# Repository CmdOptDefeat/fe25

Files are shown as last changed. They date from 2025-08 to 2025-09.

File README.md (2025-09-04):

<picture>
  <source media="(prefers-color-scheme: dark)" srcset="https://github.com/CmdOptDefeat/fe25/blob/main/repo-assets/logo/ctrlaltdefeat-no-glow-no-bg-4096.png">
  <source media="(prefers-color-scheme: light)" srcset="https://github.com/CmdOptDefeat/fe25/blob/main/repo-assets/logo/ctrlaltdefeat-no-glow-no-bg-dark-4096.png">
  CTRL+ALT+DEFEAT Logo (updates based on your theme!)
</picture>

<br><br>Welcome to the repository for our entry in the WRO Future Engineers 2025 competition!
We are a team of 2 aspiring engineers building an autonomous robotic car using Raspberry Pi 5 & RP2040, equipped with various sensors and custom designs.

# About the Team
Adbhut Patil: Adbhut is studying in 10th grade, under NIOS. He is interested in robotics, programming, and aviation.

Pranav Kiran Rajarathna: Pranav is currently studying in the 11th grade(PCMC combination) and has been interested in Robotics for several years . He has participated in WRO in other categories in the past years. He was also part of Coding club in his school and built a few robotics projects for school events. His other interests include maths, physics, numismatics and history.

| __Team Photo__ |
|:-----------:|
|Team Photo|
| __Picture: Pranav (Left) and Adbhut (Right)__ |

# Project Overview
This project is our official entry for the Future Engineers category at the World Robot Olympiad 2025. Our goal is to construct a self-driving vehicle capable of navigating the track in both the Open and Obstacle Rounds. The programs are written in C++ and Python in the VSCode IDE, with the PlatformIO extension. OpenCV is used with the Raspberry Pi for object detection and navigation. This repository contains the programs, hardware description, schematics and design files of our solution.

Note: The whole readme file is massive.
See [this section](https://github.com/CmdOptDefeat/fe25?tab=readme-ov-file#peripherals-interface-board) for more details about the peripherals interface board, and [this section](https://github.com/CmdOptDefeat/fe25?tab=readme-ov-file#raspberry-pi-system) for details about the RPi 5 and its setup. [System architecture](https://github.com/CmdOptDefeat/fe25?tab=readme-ov-file#system-architecture) includes information about the [robot and mobility](https://github.com/CmdOptDefeat/fe25?tab=readme-ov-file#mobility), [power system](https://github.com/CmdOptDefeat/fe25?tab=readme-ov-file#power), [sensors](https://github.com/CmdOptDefeat/fe25?tab=readme-ov-file#sensors), [obstacle management](https://github.com/CmdOptDefeat/fe25?tab=readme-ov-file#obstacle-management) and [parking and unparking](https://github.com/CmdOptDefeat/fe25?tab=readme-ov-file#unparking-and-parking).

Some photos of the robot - 
<br><br>
Top view
Side view
<br><br>
All photos may be found [here](https://github.com/CmdOptDefeat/fe25/tree/main/repo-assets/raw-photos/robot)

# Hardware Components
- __Compute:__ Raspberry Pi 5 (main computer), Raspberry Pi 2040 (Waveshare RP2040-Zero, real-time control)
- __Sensors:__ 1D LiDAR, IMU, rotary encoders, Picamera
- __Actuators:__ N20 geared DC motor with encoder, MG996R 180° servo
- __Chassis:__ Commercially available base with 3D-printable additions (3D-design files included)
- __Electronics:__ Custom peripherals interface PCB for reliable connections to sensors

# Repository Structure
- [design-files](https://github.com/CmdOptDefeat/fe25/tree/main/design-files) : Contains the Bill of Materials, 3D-printable design files and hardware. 
- [initial-tests](https://github.com/CmdOptDefeat/fe25/tree/main/initial-tests) : Intial tests on various sensors to ensure accurate data collection and basic object detection algorithm.
- [hw](https://github.com/CmdOptDefeat/fe25/tree/main/hw) : Contains schematic and PCB files for the peripherals interface board.
- [sw](https://github.com/CmdOptDefeat/fe25/tree/main/sw) : Contains PlatformIO project for the peripherals interface board.
- [open-round](https://github.com/CmdOptDefeat/fe25/tree/main/open-round) : It contains the program files for the open round over various iterations and hardware setups. The final open round program is found in `sw/peripherals-board/src/divers`
- [repo-assets](https://github.com/CmdOptDefeat/fe25/tree/main/repo-assets) : It contains pictures and description of the robot and its components. All other photos in the repo are also found here.
- [obstacle-round](https://github.com/CmdOptDefeat/fe25/tree/main/obstacle-round) : Programs for the obstacle round. These are categorised in order of working alphabetically. The related videos and log files are also present in these folders.
- [test-data-recordings/open-round](https://github.com/CmdOptDefeat/fe25/tree/main/test-data-recordings) : It contains data logs from various open round tests

> [!NOTE]
> Random files called `.lgd-nfy0` may be seen sometimes in varioues places. These were probably created by a typo a long time ago, and despite repeated deletion, they keep spawning everywhere in the Pi's clone of the repo! Just ignore them, if they occur. 
> `.DS_Store` are some system files used on MacOS. These too may appear throughout the repo, and may be ignored.

# System Architecture 

-	Raspberry Pi 5: It uses opencv and serial to handle the complex tasks of object detection and navigation.
-	RP2040 (Pi Pico): Handles real-time tasks (motor PID, encoder feedback, servo control, IMU, 1D LiDAR)
-	LiDARs: Used for detecting turn direction and executing turns and in parking
-	IMU: Gives yaw (and other orientations) of the robot in [0,360) clockwise
-	Motor/Servos: PWM and PI controls respectively for movement using sensor data, coordinated by the RP2040

## Mobility

- A commercially available metal [chassis base](https://www.elecrow.com/4wd-smart-car-robot-chassis-for-arduino-servo-steering.html) has been used with custom designed and printed parts. This chassis was selected mainly for its good steering system, mobility and customisabilty (there are lots of through holes through the base-frame). While the steering was retained, the remaining parts were custom designed.
- A link based steering system is used in the robot with a link-rod between the front wheel joints and another between a wheel joint and the servo. This steering system has been taken from the chassis without much modification due to its precision. A MG996R 180° servo has been used for the steering due to its high torque and accuracy, which improve mobility. The turn radius is around 32-33cm.
- Steering System
- A single axle rear drive train is used for driving is used. A 200RPM N20 motor is used due to its speed and decent torque. A 1:1 gear ratio is used with a pair of brass gears. Bearings are used on the rear axle for smooth movement. A custom [rear drive holder](https://github.com/CmdOptDefeat/fe25/blob/main/design-files/N20%20Motor%20Holder.stl) is used to house all these parts.
- Both the servo and N20 motors are connected to the peripherals board. The servo is controlled using the standard library, while PWM is used for speed control of the motor.
- Rear Drive
- This robot offers realistic car-like dynamics, ideal for FE challenge simulation.
[Design files](https://github.com/CmdOptDefeat/fe25/tree/main/design-files) contains all the other custom 3D-Design files (created on [TinkerCAD](https://www.tinkercad.com)) for mounting various compnents and systems onto the base chassis and one another.
[Robot assembly](https://github.com/CmdOptDefeat/fe25?tab=readme-ov-file#robot-assembly) instructions are below.
- Improvements: 
1. A uniform steering system. In the current model, the servo has to turn a greater angle left than right for the same angles of the wheels in each direction. This complicates driving algorithms to some extent. A better, but equally smooth steering system, maybe a rack-and-pinion, will solve these issues.
2. Better gear train. The current gears, though made of brass wear down quite easily for some unidentified reason. This causes slipping if there is more wear.
3. Reducing the turning radius. The current bot, while quite manoeuvrable has a large turn radius (almost 33-34cm). Reducing this would make taking tighter turns possible, improving error margins in the obstacle round. This can be done by bringing the drive train forward.

## Power

- A [Waveshare UPS Hat E](https://www.waveshare.com/wiki/UPS_HAT_(E)) is used for powering the robot. It uses 4 4000mAH 3.6V 21700 Li-ion batteries. (Different battery capacities may be used). All outputs are at 5V.
- The Pi is powered at a stable 5V via the POGO pins on the UPS Hat. The PiCamera and RPLidar are power from the Pi.
- The RP2040 and all connected sensors are powered through a USB A-C cable from the Pi to it.
- The total current draw for the obstacle round is around 600-630mA, and around 250-300mA for idle with the Pi.
- The peripherals board gets power directly from the UPS Hat through a USB-A cable that has been cut to get the power wires. This powers only the rear motor and steering servo.
- Improvements:
1. The UPS Hat that we are using has a weird anomaly. Although the batteries will have good voltage output and detected capacity, it will show the net remaining capacity to be very low. We have edited the code of the UPS library to not allow it run `sudo poweroff` when it misdetects such a situation.
Additiionally, charging of batteries when the Pi is off does not seem to be detected. 

## Sensors

- __TFLuna LiDAR:__ These are 1D-LiDARs that are used to measure distances to the front, left, right (for driving) and back(parking) of the robot. They are connected to the RP2040. A separate section has been designed at the front of the robot to house all four LiDARs. Each LiDAR has 5 wires, grouped into 4+1 (I2C + GND) going into the peripherals board. These LiDARs were selected for their accuracy, small size and ease of use.
- __BNO055:__ This is the IMU we are using for orientation due to its reliability, accuracy and simplicity of use. It is connected to the RP2040, and is directly slotted into the peripherals board.
- __nRF24L01:__ This is the wireless module used for wireless communication during testing and debugging with the RP2040. Another custom module (telemetry board) is made for receiving the data. (Note : This is not plugged in for actual rounds). It is directly slotted into the peripherals board.
- __Motor encoders:__ The encoders give ticks each time they are trigerred by rotation of the motor shaft. Data from it is used for distance calculations. In our case, about 43 ticks corresponds to 1cm. The 4 encoder wires are grouped together and connected to the peripherals board.
- __Raspberry Pi Camera Module 3 Wide:__ It is used with the Pi for detecting the an obstacles. The camera is secured at four points for greater stability. With only two connection points, the camera could be easily turned due to the material properties of the Camera to Pi 5 connection wire. The higher mounting location allows it to detect obstacles from a large distance (almost 2m!) and plan accordingly. The Wide lens allows for a greater field of view. The NoIR version used to give odd red patches due to the lack of the IR filter in some test cases.
- Improvements: 
1. The 1D LiDARs are quite expensive. Ultrasonic sensors would have done for the sides.
2. The BNO055 does clock stretching, which causes issues on the I2C buses of most microcontrollers (thankfully not the RP2040). It also has a slight drifting tendency of a few degrees after a round. A IMU that does not have these issues and is easy to use will be more accurate and more flexible in use.

The [Bill of Materials](https://github.com/CmdOptDefeat/fe25/blob/main/design-files/Bill%20of%20Materials.md) contains all necessary parts/components and their sources.

## Obstacle Management

- This is done mainly using the camera feed from the PiCamera 3 Wide. The NoIR version tends to give red spot in places with lots of light due to lack of IR filter, which made it incompatible for this case.
- The obstacle management sections were not able to be integrated with one another in time, but the various sections do work independently.
- The OpenCV library (in Python3) is used for all the image manipulation and data extrapolation. HSV mode has been used for all the detecting, while images arer displayed in RGB. Sometimes, red may appear as blue due to use of BGR format used by camera to record. This is of no consequence, since it does not affect detection itself.
- Initially, the colour ranges for the obstacles, parking walls and side walls are identified. Interestingly, in our case, the 'magenta' parking walls show up as pure red.
- First, the region of interest (ROI) is taken as the bottom half of the feed (this is for our camera placement. May vary for other setups).
- Then, coloured masks (one each for red and green) are applied, followed by OpenCV's controur detection to detect surfaces. Data like position, height and width of the contours may be obtained from the other OpenCV methods.
- If the contours detected meet the required criteria (like size, height-width ratio), they are classified as obstacles. For our benefit, rectangles are drawn around the obstacles.
- The basic idea is to treat both possible positions in a row of the 2x3 grid as the same (calculations use the actual values). This greatly simplifies tthe program, since only the outer and inner lanes are used for the driving, while the middle lane is used only for switching between the other two.
- Using the data available, including obstacle position, yaw and distance travelled, the required steering is calculated to pass the obstacle on the correct side, when not at a turn (Red - right, green - left) on a linear scale
- For turns:
1. Starting closer to the inner wall: The seen obstacle before the turn is considered. If turn must to taken sticking to the inner wall, it is immediately taken. If the turn must be taken to get closer to the outer wall, a curve(like a question-mark) is followed. If there is another obstacle of the opposite colour, then the robot the goes back some distance to be able to do the manoeuvre.
2. Starting closer to the outer wall: A turn is taken, making it align with the middle lane. Following this, the robot manoeuvres based on the obstacle/s present.
3. In case of the parking wall being there on every 4th turn, the turning and linear coefficients are changed to get the robot to turn to the adjusted lanes and obstacle position.

Improvements:
1. The RPLidar might have been used effectively with better drivers with the standard Raspbian OS.
2. A smaller robot would have been more agile, making both turning and straight section navigation much easier.
3. Having the axles closer would enable for tighter turns.

## Getting out of the parking lot
Getting out of the parking lot (fondly referred to as "unparking") is handled by the peripherals interface board. The vehicle takes three turns to orient itself so it is perpendicular to the parking lot, and then backs up into the parking lot. It then transfers control to the Raspberry Pi.

## Parallel parking
Parking is also handled by the peripherals interface board. The Raspberry Pi hands over control after the last obstacle. The algorithm takes the following steps:
- Move backwards until the vehicle is abeam the parking lot
- Turn and move backwards and move into the parking lot
- Move forwards so that the next turn can be made
- Turn and move backwards into the parking lot
- Move forwards and turn until the vehicle is parallel to the parking lot

# Robot Assembly

It will be helpful to refer to the [pictures of the construction](https://github.com/CmdOptDefeat/fe25/tree/main/repo-assets/raw-photos/assembly) while building. Most screws used are of 3M type (3mm dia.). At some places in our robot, internal hex screws are used in places where plus(+) screws of the right length were not available.
1. Add the front wheels and steering link to the robot
2. Attach the servo motor and connect it to the steering link
3. Print all design files
4. Attach the N20 motor onto the rear drive with brackets. Fit a gear onto the motor.
5. Cut the rear axle to the appropriate length (around 96mm) and attach the rear axle with wheels and gear onto the rear drive.
6. Mount the rear drive onto the chassis.
7. Attach 6 pillar screws of length 26mm in the back and 2 of length 22mm in the front (adjacent to the servo)
8. Attach the middle plate at the 6 rear points, but not at the front. The peripherals board may be screwed on using 4 pillar screws.
9. Attach the TFLuna LiDARs to the front LiDAR holder section.
10. Attach the LiDAR holder section to the front of the chassis.
11. Attach the additional support section (this used to be used when the RPLidar was also attached to the model) to the 2 front middle plate points and 2 rear RPLidar points.
13. Attach the two PiCamera holder parts to the rear of the support section, and screw in the camera (2M screws and nuts are needed)
12. Attach the top-most Raspberry Pi and UPS platform to the rear with screw pillars.
13. Attach the rear lidar holder with the rear lidar attached to it
14. Attach the Raspberry Pi with the UPS Hat to the top.
15. Make all wired connections by referring to schematic files.

# Peripherals Interface Board
Peripherals Interface Board - Top

The peripherals interface board goes between the Raspberry Pi and vehicle hardware. The board talks to three 1d TFLuna LiDARs, a 9-axis BNO055 IMU, the motor encoder, the drive motor, and the steering servo. It talks to the Pi over USB.

Peripherals Board on the Robot

## Hardware
The board is a two-layer, 1.6 mm thick PCB designed in [KiCad](https://kicad.org) and manufactured by [Robu](https://robu.in).
TODO: Expand

## Software
The interface board was programmed in C++, with the C++ SDK from Raspberry Pi for the RP2040 chip. Code was compiled and flashed with the PlatformIO extension for Visual Studio Code.

The codebase is designed to be modular, with easily swappable drivers for hardware abstraction. Algorithms do not need to know about specific hardware protocols or constraints

`main.cpp` loads in drivers, which implement virtual interface classes. `main.cpp` then initialises everything, and in a loop, gets data from the `SensoorManager`, passes that data to our drive algorithm, and outputs it to the `TargetController`, which commands the motor and steering servo.
Drivers are in `/src/drivers`, Interfaces are in `/src/interfaces/`, and utilities are in `/src/utils/`.

### Code Development Standards
To ensure easily testable, upgradeable, and clean code, the following standards were decided for writing code for the interface board.
> [!NOTE]
> Due to time constraints, not all of these could be adhered to during final development

- `main.cpp` must be as clean as possible.
- Logic and code flow must be easy to understand.
- All hardware-specific things should be done inside a driver.
- Drivers must take in a standard unit as their input.
- Drivers must not take in [magic numbers](https://en.wikipedia.org/wiki/Magic_number_(programming)).

### Drivers
> [!NOTE]
> Hardware revision 1 drivers are incomplete, as the peripherals baord codebase was partly written when the switch from the prototype interface and the PCB occured, and drivers from that point on were only for the PCB (hardware revision 2).

A list of implemented drivers:
- `hwrev2_imu` : Implements `ISensor`. Driver for the BNO055. Gets orientation data processed by the BNO055's internal microcontroller.
- `hwrev2_lidar` : Implements `ISensor`. Driver for the TFLuna LiDARs. Returns a [0, 359] of distance data. The three LiDARs are mapped to `0`, `90`, and `270`. (This is a remnant of the original plan of connecting the RPLidar to the peripherals board, instead of to the Pi.)
- `hwrev2_motor_driver` : Implements `IMotorDriver`. Driver for the TB6612FNG dual-channel H-bridge motor driver. The driver only supports driving a single channel on the T66612FNG.
- `hwrev2_rf24_communication` :  Implements `ICommunication`. Driver for the nRF24L01+ radio used during development. Transmits vehicle data and gets commands from another nRF24L01+, connected to a computer.
- `hwrev2_single_lidar_open_round` : Implements `IDriveAlgorithm`. A port of our open round test algorithm. The name is misleading, the algorithm uses all three TFLunas.
- `hwrev2_steering_driver` : Implements `ISteeringDriver`. Driver for the MG996 steering servo. Takes in a degree input and coverts it to a 0-180 command with a conversion constant.
- `hwrev2_target_control` : Implements `ITargetControl`. Takes in a `VehicleCommand`, and either passes it directly through to the `ISteeringDriver` and `IMotorDriver`, or passes the command through a PID controller first.
- `hwrev2_uart_logger` :  Implements `ILogger`, Takes in a sender, message type, and a message string
- `hwrev2_vehicle_speed` : Implements `ISensor`. Gets vehicle distance from the motor encoder. Calculates speed using time between pulses.
  TODO: unparking and parking drivers

### Interfaces

Interfaces are virtual classes which define certain functions. Drivers implement these classes. Code calls functions defined in the virtual interface class.

- `IDriveAlgorithm` : Takes in a `VehicleData` object, and returns a `VehicleCommand` object.
- `ILogger` : Constructs a message and prints it out on a UART bus. Takes in a sender string, a log type (information, warning, error) and the message.
- `IMotorDriver` : Takes in a speed value and outputs to a motor driver.
- `ISensor` :  A generic sensor object. Returns a vector of `SensorData` objects.
- `ISteeringDriver` :  Takes in a wheel steering angle, outputs to a steering mechanism.
- `ITargetControl`: Takes in a `VehicleCommand`, outputs to a motor and steering driver.

### Managers

Managers are classes that handle certain aspects of the vehicle. Certain structs have their header files in the `/src/managers` folder, even though they are not classes.

- `VehicleConfig` :  A struct containing information about the vehicle. A `VehicleConfig` struct is passed to all drivers asnd managers.
- `SensorData` :  A struct containing fields for all data that can be collected by the vehicle, and an enum which tells the caller what fields are being used.
- `SensorManager` :  A class which takes in an arbitrary number of sensors, collects data from them, and processes them into a `VehicleData` struct.
- `SensorStatus` :  A (currently unused) enumeration which defines keys for states a sensor can be in. 
- `Vec3f` :  A struct of three double-precisionn floating point numbers, used to represent three-axis values.
- `VehicleCommand` :  A struct defining a target speed and yaw value for the vehicle. Returned by a drive algorithm, passed to a `ITargetController`.
- `VehicleData` :  A struct containing processed vehicle data. Returned by a `SensorManager`.

## Utilities

- `SchedulerTask` : A class which calls a function periodically.
- `Schedular` : A class which takes in an arbitrary number of `SchedulerTask`s, and updates them.

# Raspberry Pi System

The Raspberry Pi system handles most tasks for the obstacle round, including unparking, obstacle detection and navigation.
TODO: it doesn't handle unparking, update this section

## Raspbian Setup

We are using Raspbian Bookworm on the Raspberry Pi (latest at the time of this project)
Run the following commands in the terminal
- $`sudo chmod 0700 /run/user/1000`
- $`sudo apt install software-properties-common`
- $`sudo apt install python3-launchpadlib`
- $`sudo apt install code`
- $`sudo apt upgrade code`
- $`sudo apt install idle3`
- $`sudo apt install python3-opencv`
- $`sudo apt install -y python3-libcamera python3-pyqt5 python3-picamera2`
- Test camera library installation with $`rpicam-hello`
- Refer [here](https://www.waveshare.com/wiki/UPS_HAT_(E)) to install UPS Hat library to see details about the batteries etc.
- If the Pi is accidentally shut down, and git is not working, run the following commands: 
1. $`find .git/objects/ -type f -empty | xargs rm` - Cleaning
2. $`git fetch -p` - Restore missing objects
3. $`git fsck --full` - Verify
- It is advised to have RPiConnect for easy connection to the Pi.
- This reposittory is cloned on the Pi and the obstacle round program is added to the startup sequence.

## Adding Programs to Startup

The method used here involves running executables on startup. Refer [`initial-tests/startup-test/`](https://github.com/cmdoptdefeat/fe25/tree/main/initial-tests/startup-test) for the code.
1. Create the python file
2. Create a launcher script, like the one in the initial test file, that ends in `.sh`. Ensure the launcher is working with `./(launcher-name).sh` in its directory.
3. In the launcher script, navigate to the directory of the python file and run it with `sudo python3 (file-name).py`. Then return to user directory
4. In the directory with launcher script, make it executable by running `sudo chmod 755 (launcher-name).sh`
5. Run `sudo crontab -e` (you can use nano to edit it), and add `@reboot sh /home/(user)/(path to launcher)/(launcher-name).sh` at the end.
6. Restart the Pi (`sudo reboot`) to check if it works. 

## PiCamera 3

The Raspberry Pi Camera Module 3 Wide is used for obstacle detection. It is placed high up to have a good view. (We actually only use the bottom half of the frame!) It is connected to port 0.

## Serial Communication

The Pi communicates with the RP2040 over the serial. When the Pi sends a command (speed and steering), the RP2040 sends back data (like yaw, lidar distance, turn direction etc.) The RP2040 is connected to a USB port of the Raspberry Pi and is recognised by its ID.

# Open Round

Refer to [`sw/peripherals-board/src/drivers/hwrev2/hwrev2_single_lidar_open_round.cpp and .hpp`](https://github.com/CmdOptDefeat/fe25/blob/main/sw/peripherals-board/src/drivers/hwrev2/hwrev2_single_lidar_open_round.cpp) files for program.
The idea to stick to the outer wall, so even with randomisation, the extended inner wall is not hit.

Videos of the open round may be found [here](https://github.com/CmdOptDefeat/fe25/tree/main/repo-assets/open-round-videos)

- Uses front LiDAR to detect when to start a turn (if obstacle is close).
- Decides turn direction (left/right) based on side LiDARs (First turn only)
- Turns are started considering factors of distance available, yaw, current section and distance travelled. 
- Adjusts steering (servo position) during turn based on yaw and for greater smoothness.
- Target yaw and threshold distance may be altered for better accuracy and counter drifting.
- When not turning, PI controller is used with yaw to follow a straight path accurately.
- Counts turns; after 12 turns (3 rounds), slows down and stops at the start section.

## Flow
1. Start moving straight.
2. Decide turn direction using side LiDARs. (For first turn only)
3. Detect distance to wall ahead with front LiDAR.
4. Execute turn when condition are met, adjust steering and target yaw.
5. After turn, resume straight movement with PI control.
6. Repeat for 3 rounds (12 turns).
7. After final round, slow down and stop in the start section.

# Acknowledgements

We would like to thank
- YoLabs Team: We thank the YoLabs Team for their guidance and mentorship provided, which helped us improve algorithms and robot design.
- Raspberry Pi Foundation: Gratitude is owed to the Raspberry Pi Foundation for making excellent hardware, enabling development of this project.
- OpenCV: Appreciation goes to the OpenCV community for supplying the computer vision tools and extensive documentation, which we have used and are crucial to the solution for the obstacle round.
- GitHub: Recognition is given to GitHub for providing a collaborative platform that streamlined code management and teamwork, ensuring efficient  development.

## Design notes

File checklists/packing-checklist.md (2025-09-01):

# Packing Checklist

## Pranav
- Screwdrivers (yellow kit + Amazon Basics)
- Allen key set + allen screwdrivers
- Hex turner + Hex screwdrivers
- Struts + screws box x2
- Wire stripper - red + cutter - blue
- Pliers
- Tweezers
- Crimping kit
- 3-Partition box
- RPi5 16GB with spare SD Card
- Spare Camera wire
- Spare USB-A wire to cut
- Spare 21700 batteries x4
- Spare Lidar cables x2
- Gears x2
- Spare USB-A to USB-C wire for serial communication
- Spares of all 3D-printed parts
- Spare N20 motor x2
- Spare servo motor - MG996R x2
- Jumper wires
- Powerbanks

## Adbhut
- USB-A to USB-C cable
- USB-A to USB-Mini cable
- USB-C to USB-C cable
- Peripherals Interface Spare Parts
- Peripherals Interface development hardware

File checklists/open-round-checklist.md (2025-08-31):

# Open Round Checklist
## Things to do right before / as vehicle is powered up for the open round

### Before round starts
| Item | Action |
| ---- | --- |
| RPi UPS Module batteries | Fully insert |
| RPi UPS Module power switch | Off |
| Peripherals Interface power switch | On |

### Powering vehicle on
| Item | Action |
| ---- | --- |
| RPi UPS Module power switch | On |
| Peripherals Interface start button | Press |

### Peripherals Interface LED Colors
| Color | State | Indication |
| ----- | ----- | --- |
| Blue | Steady | Sensors are being calibrated
| Green | Steady | Sensors are calibrated, Peripherals Interface has control |
| Green | Blinking | RPi 5 has control |
| Amber | Blinking | Sensors failed to calibrate/are not detected

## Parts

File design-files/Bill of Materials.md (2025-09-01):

# Bill of Materials

## Chassis
| Item | Part No. | Quantity | Notes/Description | Link | 
|:---:|:---:|:---:| :---:| :---:|
| N20 Motor Mounting Bracket | - | 1 | Hold N20 motor in place in the rear drive section | [Product Link](https://robu.in/product/mounting-bracket-n20-micro-gear-motors) |
| Gears | Metal 24 tooth spur gear, 3mm | 2 | Used in the rear drive | [Product Link](https://robu.in/product/metal-48p-spur-gear-24t/) |
| Rear Drive Section | Custom design | 1 | Holds rear axle and N20 motor and connection through gear | [Link to Design](https://github.com/pkr2308/Ctrl-Alt-Defeat-WRO-Future-Engineers-2025/blob/main/Design%20Files/N20%20Motor%20Holder.stl) |
| Shaft | 3mm | 1 | Used as rear drive shaft |
| Chassis | RBP68138C | 1 | Front steering and single axle rear drive | [Product Link](https://www.elecrow.com/4wd-smart-car-robot-chassis-for-arduino-servo-steering.html) |
| 18650 Batteries | 3.7 V Different mAH options availaible | 2 | Provide power | [Product Link](https://robu.in/product/dmegc-inr18650-26e-3-7v-2600mah-li-ion-battery) |
| 21700 Batteries | 3.6 V Used with UPS Hat to power the Pi | 4 | Provide power | [Product Link](https://robu.in/product/bak-nmc-n21700cgp-3-6v-4000mah-10c-li-ion-battery) |
| Battery Holder | - | 1 | Hold the 18650 batteries, and has an on/off switch | [Product Link](https://robu.in/product/18650-x-2-battery-holder-with-cover-and-on-off-switch) |
| Custom Designed Parts | - | 1 each | Used for attaching various components to the robot |[Design files](https://github.com/pkr2308/Ctrl-Alt-Defeat-WRO-Future-Engineers-2025/tree/main/Design%20Files) |
| Miscellaneous | - | - | Wires, Screws, Pillar Screws etc. | [Pillar Screws](https://robu.in/product/pro-range-120pcs-m3-hexagon-copper-pillar-screw-kit/) |

## RP2040 System
| Item | Part No. | Quantity | Notes/Description | Link | 
|:---:|:---:|:---:| :---:| :---:|
| RP2040 | Waveshare RP2040-Zero | 1 | Real time control of motors, sensors | [Product Link](https://robu.in/product/waveshare-rp2040-zero-without-header/) |
| Peripherals Board PCB | Custom design | 1 | Reliable connections between peripherals and peripherals interface board | [Link to Design](https://github.com/pkr2308/Ctrl-Alt-Defeat-WRO-Future-Engineers-2025/tree/main/hw/peripherals-board-v2) |
| 1D LiDAR | Benewake TF-LUNA Micro | 4 | Finding distances to front, sides and back of robot | [Product Link](https://robu.in/product/benewake-tf-luna-lidar-distance-sensor/) |
| 1D LiDAR Connectors | 28AWG 1.25mm 6 Pin Female Connector | 4 | Connect LiDAR to peripherals board | [Product Link](https://robu.in/product/a1251-06y-1-25mm-6-pin-female-housing-connector-with-300mm-wire30-awg/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) |
| IMU | BNO055 | 1 | Obtaining yaw readings | [Product Link](https://thinkrobotics.com/products/9-dof-absolute-orientation-bno055-sensor) |
| Wireless Radio Transciever (Optional) | NRF24L01 Wireless Transceiver | 1 | Wireless communication during testing and debugging | [Product Link](https://robu.in/product/m177-nrf24l01-2-4ghz-antenna-wireless-transceiver-module)
| Motor Driver Board | TB6612FNG | 1 | Control N20 Motor | [Product Link](https://robu.in/product/motor-driver-tb6612fng-module-performance-ultra-small-volume-3-pi-matching-performance-ultra-l298n/) |
| Motor with Encoder | N20 6V 200RPM Micro Metal Gear Motor With Encoder | 1 | Rear driving motor | [Product Link](https://robu.in/product/n20-6v-200rpm-micro-metal-gear-motor-with-encoder/) |
| Servo Motor | MG996R 180° | 1 | For steering | [Product Link](https://robocraze.com/products/mg996r-servo-motor?variant=40192896368793) |
| Wire Management | 3, 4 Pin JST-XH 2.5mm wafers and housing; DuPont 2.54mm female headers | 1, 6, 34 | Connect various components easily onto peripherals board | - |
| Screw Terminals | 2 Pin Screw Terminals | 2 | Connecting power and motor pins to peripherals board | [Product Link](https://robu.in/product/xy128vc-5-0-xinya-2-pin-screw-terminal-blockgreen) |

## Raspberry Pi 5 System
| Item | Part No. | Quantity | Notes/Description | Link | 
|:---:|:---:|:---:| :---:| :---:|
| Raspberry Pi 5 | Raspberry Pi 5 Model 8GB | 1 | Object and lane detection and route planning | [Product Link](https://robu.in/product/raspberry-pi-5-model-8gb/) |
| Cooler for Pi | Raspberry Pi 5 Active Cooler | 1 | Cool the Pi when running | [Product Link](https://robu.in/product/official-raspberry-pi-5-active-cooler) |
| Picamera | Pi Camera Module 3 - Wide | 1 | Object, colour detection | [Product Link](https://robu.in/product/raspberry-pi-camera-module-3-wide) |
| Picamera Wire | Raspberry Pi 5 Camera FPC Cable 300mm | 1 | Connects PiCamera to RPi 5 | [Product Link](https://robu.in/product/official-raspberry-pi-5-camera-fpc-cable-300mm/) |
| USB A - USB C Cable | - | 1 | Connect the Pi to the RP2040 | - |
| UPS Hat | WaveShare UPS Hat E | 1 | Used power constant 5V supply to RPi | [Product Link](https://robu.in/product/ups-hat-e-for-raspberry-pi/) |

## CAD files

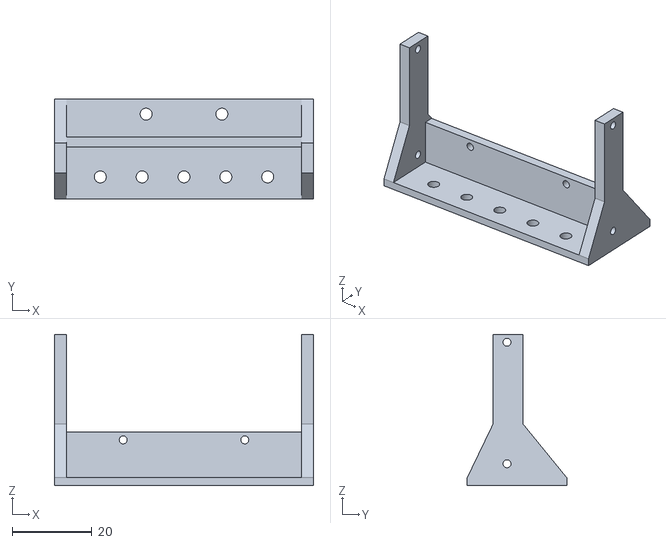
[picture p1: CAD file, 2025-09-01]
design-files/Lidar Holder V4.stl
65.0 x 25.0 x 38.0

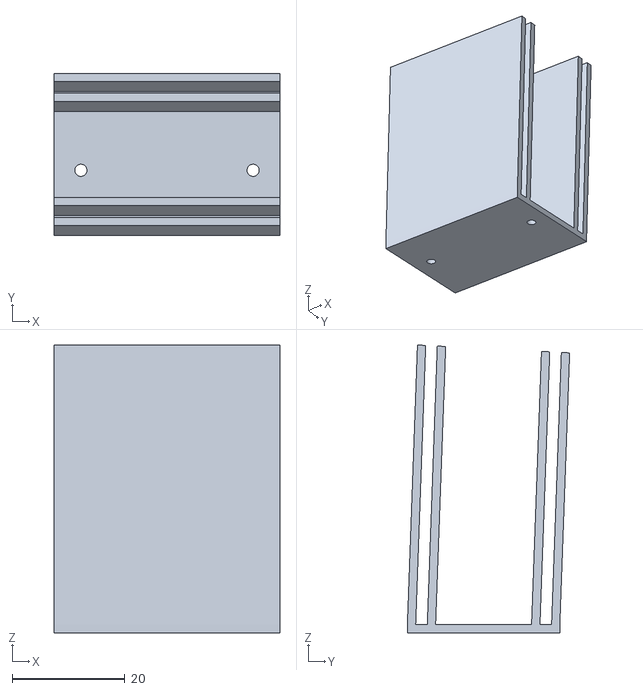
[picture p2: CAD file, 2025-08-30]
design-files/Rear Lidar Mount-Long.stl
40.0 x 28.7 x 51.0

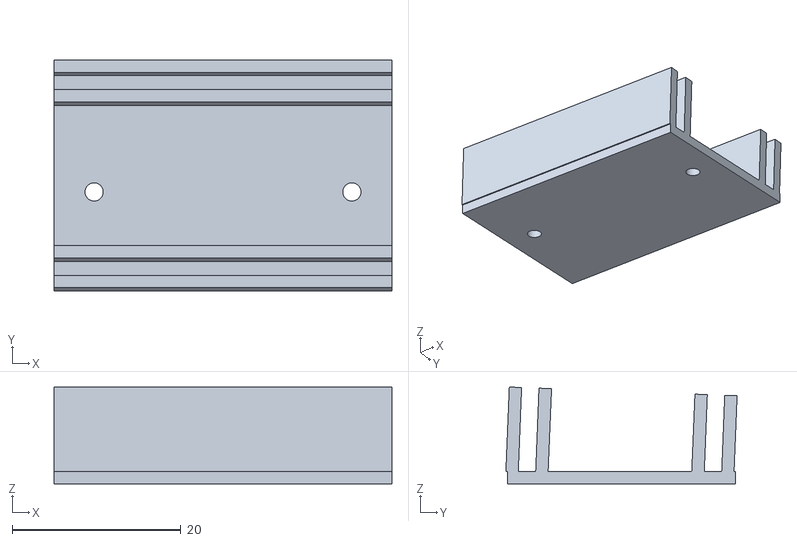
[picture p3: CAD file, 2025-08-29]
design-files/Rear Lidar Mount.stl
40.0 x 27.4 x 11.5

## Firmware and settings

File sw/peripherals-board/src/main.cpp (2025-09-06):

/**
 * @file main.cpp
 * @brief Initialises drivers and managers, handles interaction between managers
 * @author DIY Labs
 */

#include "Arduino.h"

// COMPETITION_OPEN_ROUND, COMPETITION_OBSTACLE_ROUND
//#define COMPETITION_OPEN_ROUND
#define COMPETITION_OBSTACLE_ROUND
#define VEHICLE_DRIVERSET_HWREV2                        // HWREV2 **NOTE** HWREV1 DRIVERS ARE INCOMPLETE, BUGGY, OR MISSING!!
#define VEHICLE_SW_STATUS "Competition Compile"         // String containing status of software. Printed over debug port
#define VEHICLE_SW_NAME "Competition Day 2 Unparking"   // String containing name of software. Printed over debug port

#include <driverconfig.hpp>                             // **NOTE** All config #defines must be before this include
#include <SensorManager.hpp>


VEHICLE_DRIVER_IMU bno(VEHICLE_GET_CONFIG);
VEHICLE_DRIVER_LIDAR lidar(VEHICLE_GET_CONFIG);
VEHICLE_DRIVER_SPEED speed(VEHICLE_GET_CONFIG);
VEHICLE_DRIVER_MOTOR motor(VEHICLE_GET_CONFIG);
VEHICLE_DRIVER_STEERING steering(VEHICLE_GET_CONFIG);
VEHICLE_DRIVER_TARGET_CONTROL targetControl(VEHICLE_GET_CONFIG);
VEHICLE_DRIVER_OPEN_ROUND_ALGORITHM openRoundAlgorithm(VEHICLE_GET_CONFIG);
VEHICLE_DRIVER_UNPARK_ALGORITHM unparkAlgorithm(VEHICLE_GET_CONFIG);
VEHICLE_DRIVER_PARK_ALGORITHM parkAlgorithm(VEHICLE_GET_CONFIG);
VEHICLE_DRIVER_REMOTE_COMMUNICATION remoteCommunication(VEHICLE_GET_CONFIG);
VEHICLE_DRIVER_SERIAL_COMMUNICATION serialCommunication(VEHICLE_GET_CONFIG);
//VEHICLE_DRIVER_ROS_COMMUNICATION rosCommunication(VEHICLE_GET_CONFIG);
VEHICLE_DRIVER_DEBUG_LOG debugLogger(VEHICLE_GET_CONFIG);
VEHICLE_DRIVER_RGB_LED rgbLED(VEHICLE_GET_CONFIG);
SensorManager sensorManager(VEHICLE_GET_CONFIG);


enum CoreControlState{

  WAIT_FOR_BUTTON,
  OPEN_ROUND,
  GET_ORIENTATION,
  UNPARK,
  DRIVE_FROM_PI,
  PARK,
  SAFE

};

VehicleCommand coreVehicleCommand;
bool coreVehicleCommandDirect;
VehicleCommand coreSerialCommand;
VehicleData coreVehicleData;
VehicleInstruction coreVehicleInstructionToPi;
VehicleInstruction coreVehicleInstructionFromPi;
CoreControlState coreControlState;
bool coreRoundDirCW;


void coreWaitForButton();
void coreGetOrientation();
void coreUnpark();
void coreDriveFromPi();
void corePark();
void coreSafe();
void coreOpenRound();
void coreRunStateMachine();
void coreCheckSafeButton();
void coreSetLEDColor(CoreControlState state);
String coreGetStringFromState(CoreControlState state);


void debugPrintVehicleData(VehicleData data, VehicleCommand cmd);
void debugLogHeader();
void debugLogDataCommand(VehicleData data, VehicleCommand cmd);
void debugProbeI2CAddr(byte addr);
void debugFailureBlink();
void debugKillBlink();
void debugKillCallback();
void debugRebootCallback();
void debugBootselCallback();

/**
 * @brief Initialises sensor manager, target controller, and drive algorithm
 */
void setup(){

  // Check if multiple vehicle configurations are defined when compiling
  #if (defined(VEHICLE_CONFIGURATION_OPEN_ROUND) + defined(VEHICLE_CONFIGURATION_OBSTACLE_ROUND_UNPARKING)) > 1
    #error "Multiple vehicle configuration defines are set! Only one of VEHICLE_CONFIGURATION_OPEN_ROUND or VEHICLE_CONFIGURATION_OBSTACLE_ROUND_UNPARKING should be defined."
  #endif

  #if defined(DVEHICLE_CONFIGURATION_OBSTACLE_ROUND_NO_UNPARKING)
    #error "DVEHICLE_CONFIGURATION_OBSTACLE_ROUND_NO_UNPARKING is deprecated, use VEHICLE_CONFIGURATION_OPEN_ROUND or VEHICLE_CONFIGURATION_OBSTACLE_ROUND_UNPARKING "
  #endif

  debugLogger.init();  
  debugLogger.addKillHandler(debugKillCallback);
  debugLogger.addBootselHandler(debugBootselCallback);
  debugLogger.addRebootHandler(debugRebootCallback);

  debugLogHeader();

  rgbLED.init(&debugLogger);
  rgbLED.limitBrightness(10);
  rgbLED.setStaticColor(rgbLED.BLUE);

  SPI1.setSCK(VEHICLE_GET_CONFIG.pinConfig.spi1SCK);
  SPI1.setRX(VEHICLE_GET_CONFIG.pinConfig.spi1MISO);
  SPI1.setTX(VEHICLE_GET_CONFIG.pinConfig.spi1MOSI);
  SPI1.begin();

  Serial1.setRX(VEHICLE_GET_CONFIG.pinConfig.uart0RX);
  Serial1.setTX(VEHICLE_GET_CONFIG.pinConfig.uart0TX);  

  Wire.setSCL(VEHICLE_GET_CONFIG.pinConfig.i2c0SCL);
  Wire.setSDA(VEHICLE_GET_CONFIG.pinConfig.i2c0SDA);
  Wire.begin();

  pinMode(VEHICLE_GET_CONFIG.pinConfig.lidarMotorPWM, INPUT_PULLUP);

  debugLogger.sendMessage("setup()", debugLogger.INFO, "Finished setting communication pins for SPI1, UART1, I2C0");

  unparkAlgorithm.init(&debugLogger);
  parkAlgorithm.init(&debugLogger);
  openRoundAlgorithm.init(&debugLogger);
  sensorManager.init(&debugLogger);

  if(!sensorManager.addSensor(&bno)){

    debugLogger.sendMessage("setup()", debugLogger.ERROR, "Failed to add BNO055 driver to sensor manager. Going into infinite loop.");
    
    while(true){
      debugFailureBlink();
    }

  }

  if(!sensorManager.addSensor(&lidar)){

    debugLogger.sendMessage("setup()", debugLogger.ERROR, "Failed to add TFLuna driver to sensor manager. Going into infinite loop.");
    
    while(true){
      debugFailureBlink();
    }

  }

  if(!sensorManager.addSensor(&speed)){

    debugLogger.sendMessage("setup()", debugLogger.ERROR, "Failed to add motor encoder driver to sensor manager. Going into infinite loop.");
    
    while(true){
      debugFailureBlink();
    }

  }
  
  
  debugLogger.sendMessage("setup()", debugLogger.INFO, "Finished adding drivers to sensor manager");
  rgbLED.setStaticColor(rgbLED.GREEN);

  targetControl.init(&motor, &steering, &debugLogger);
  motor.driveMotor(0, 0);
  steering.steer(0);

  remoteCommunication.init(&debugLogger);
  serialCommunication.init(&debugLogger);

  coreControlState = WAIT_FOR_BUTTON;

  debugLogger.sendMessage("setup()", debugLogger.INFO, "Setup complete");

}

/**
 * @brief Reads data from sensors, runs state machine, commands output devices
 * @author DIY Labs
 * @note Consider removing debug updates to save loop time for competition, probably not required
 */
void loop(){

  // Create gap between loop prints
  debugLogger.sendString("\n\n\n");

  // Handle any serial input over debug port (disable for competition compile?)
  //debugLogger.handleInput();

  // Get fresh data from sensors (manually set round direction bool based on what we've found out before)
  coreVehicleData = sensorManager.update();
  coreVehicleData.roundDirectionCW = coreRoundDirCW;
  coreVehicleData.instruction = coreVehicleInstructionToPi;  

  // Update state machine
  coreRunStateMachine();

  targetControl.directControl(coreVehicleCommand, coreVehicleData);

  // Log latest data and drive commands over debug serial port
  debugLogDataCommand(coreVehicleData, coreVehicleCommand);

  // Send latest data and drive commands over nRF24L01+ radio; not using any commands the telemetry adapter sends
  //remoteCommunication.update(coreVehicleData, coreVehicleCommand); 

  // Update RPi on communication, set core instruction
  //coreSerialCommand = serialCommunication.update(coreVehicleData, coreVehicleCommand);
  //coreVehicleInstructionFromPi = coreSerialCommand.instruction;

}


/**
 * @brief Function for printing all collected vehicle data without names for use with SerialPlot
 * @note Do not modify order or add name print to variables 
 * @author DIY Labs
 */
void debugPrintVehicleData(VehicleData data, VehicleCommand cmd){

  Serial.print("Yaw: ");
  Serial.print(data.orientation.x);

  Serial.print(" Distance: ");
  Serial.print(data.encoderPosition / 43);
  Serial.print(" Speed: ");
  Serial.println(data.speed);

  Serial.print(" Lidar Left: ");
  Serial.print(data.lidar[270]);
  Serial.print(" Front: ");
  Serial.print(data.lidar[0]);
  Serial.print(" Right: ");
  Serial.print(data.lidar[90]);
  Serial.print(" ");

  Serial.print(" Target Servo ");
  Serial.print(cmd.targetYaw);
  Serial.println();

}

/**
 * @brief Prints a data frame over debug port, frame contains vehicle data and  active vehicle command
 * @author DIY Labs
 */
void debugLogDataCommand(VehicleData data, VehicleCommand cmd){

  debugLogger.sendMessage("debugLogDataCommand()", debugLogger.INFO, "Data frame start");

  debugLogger.sendString(String(data.orientation.x));
  debugLogger.sendString(", ");
  debugLogger.sendString(String(data.orientation.y));
  debugLogger.sendString(", ");
  debugLogger.sendString(String(data.orientation.z));
  debugLogger.sendString(", ");

  debugLogger.sendString(String(data.acceleration.x));
  debugLogger.sendString(", ");
  debugLogger.sendString(String(data.acceleration.y));
  debugLogger.sendString(", ");
  debugLogger.sendString(String(data.acceleration.z));
  debugLogger.sendString(", ");

  debugLogger.sendString(String(data.angularVelocity.x));
  debugLogger.sendString(", ");
  debugLogger.sendString(String(data.angularVelocity.y));
  debugLogger.sendString(", ");
  debugLogger.sendString(String(data.angularVelocity.z));
  debugLogger.sendString(", ");

  debugLogger.sendString(String(data.encoderPosition));
  debugLogger.sendString(", ");

  debugLogger.sendString(String(data.speed));
  debugLogger.sendString(", ");

  debugLogger.sendString(String(data.lidar[0]));
  debugLogger.sendString(", ");
  debugLogger.sendString(String(data.lidar[90]));
  debugLogger.sendString(", ");
  debugLogger.sendString(String(data.lidar[180]));
  debugLogger.sendString(", ");
  debugLogger.sendString(String(data.lidar[270]));
  debugLogger.sendString(", ");

  debugLogger.sendString(String(cmd.targetSpeed));
  debugLogger.sendString(", ");
  debugLogger.sendString(String(cmd.targetYaw));
  debugLogger.sendString(", ");

  debugLogger.sendString("\n");

  debugLogger.sendMessage("debugLogDataCommand()", debugLogger.INFO, "Data frame end");

}

/**
 * @brief Prints sw versions over debug port
 * @author DIY Labs
 */
void debugLogHeader(){

  debugLogger.sendMessage("debugLogHeader()", debugLogger.INFO, "CTRL+ALT+DEFEAT Peripherals Board Debug Port");
  debugLogger.sendMessage("debugLogHeader()", debugLogger.INFO, "Software status: " + String(VEHICLE_SW_STATUS));
  debugLogger.sendMessage("debugLogHeader()", debugLogger.INFO, "Software name: " + String(VEHICLE_SW_NAME));  
  debugLogger.sendMessage("debugLogHeader()", debugLogger.INFO, "Compiled on: " + String(__DATE__) + " at: " + String(__TIME__));
  debugLogger.sendMessage("debugLogHeader()", debugLogger.INFO, "Pico SDK version: " + String(PICO_SDK_VERSION_STRING));

}

/**
 * @note Sometimes doesn't return a success, even when device works. Don't have time to debug it now. Check data stream over debug to ensure sensors are alive.
 */
void debugProbeI2CAddr(byte addr){
    
  Wire.beginTransmission(addr);
  byte err = Wire.endTransmission();

  String errStr;

  switch(err){
    case 0:
      errStr = "Success";
      break;

    case 1:
      errStr = "Data too long";
      break;

    case 2:
      errStr = "NACK on transmit of address";
      break;

    case 3:
      errStr = "NACK on transmit of data";
      break;

    case 4:
      errStr = "Other error";
      break;

    case 5:
      errStr = "Timeout";
      break;

    default:
      break;
    
  };

  debugLogger.sendMessage("debugLogHeader()", debugLogger.INFO, "Error for address " + String(addr, HEX) + " is " + errStr);

  delay(5);

}

/**
 * @brief Blinks onboard LED amber (BLOCKING!)
 */
void debugFailureBlink(){

  rgbLED.limitBrightness(50);
  rgbLED.setStaticColor(rgbLED.AMBER);
  delay(100);
  rgbLED.setStaticColor(rgbLED.BLACK);
  delay(100);

}

void debugKillBlink(){

  rgbLED.limitBrightness(50);
  rgbLED.setStaticColor(rgbLED.CYAN);
  delay(50);
  rgbLED.setStaticColor(rgbLED.BLACK);
  delay(1000);

}

void debugKillCallback(){

  debugLogger.sendMessage("debugKillCallback", debugLogger.INFO, "Kill callback called. Entering safe state.");

  coreSafe();

  while(true){
    debugKillBlink();
  }

}

void debugRebootCallback(){

  rp2040.reboot();

}

void debugBootselCallback(){

  rp2040.rebootToBootloader();

}

void coreWaitForButton(){
  coreVehicleCommand.targetYaw = 90;
  coreVehicleCommand.targetSpeed = 0;
  coreVehicleCommandDirect = true;

  #if defined(VEHICLE_CONFIGURATION_ENABLE_BUTTON_CHECK)

    if(digitalRead(VEHICLE_GET_CONFIG.pinConfig.lidarMotorPWM)){
      return;
    }

  #endif


  #if defined(VEHICLE_CONFIGURATION_OPEN_ROUND)
    debugLogger.sendMessage("coreUpdateButton", debugLogger.INFO, "VEHICLE_CONFIGURATION_OPEN_ROUND defined.");
    coreControlState = OPEN_ROUND;
    rgbLED.setStaticColor(rgbLED.PURPLE);
    delay(1000);
    debugLogger.sendMessage("coreWaitForButton()", debugLogger.INFO, "Button press detected. Setting coreControlState to OPEN_ROUND");
  #elif defined(VEHICLE_CONFIGURATION_OBSTACLE_ROUND_UNPARKING)
    debugLogger.sendMessage("coreUpdateButton", debugLogger.INFO, "VEHICLE_CONFIGURATION_OBSTACLE_ROUND_UNPARKING defined.");
    coreControlState = GET_ORIENTATION;\
    rgbLED.setStaticColor(rgbLED.PURPLE);
    delay(1000);
    debugLogger.sendMessage("coreWaitForButton()", debugLogger.INFO, "Button press detected. Setting coreControlState to GET_ORIENTATION");
  #else
    #error "VEHICLE_CONFIGURATION_OPEN_ROUND, VEHICLE_CONFIGURATION_OBSTACLE_ROUND_NO_UNPARKING, or VEHICLE_CONFIGURATION_OBSTACLE_ROUND_UNPARKING must be defined!"
  #endif

}

void coreGetOrientation(){

  uint16_t leftDist = coreVehicleData.lidar[270];
  uint16_t rightDist = coreVehicleData.lidar[90];

  coreRoundDirCW = rightDist > leftDist;

  #if defined(VEHICLE_CONFIGURATION_OBSTACLE_ROUND_UNPARKING)
    debugLogger.sendMessage("coreGetOrientation", debugLogger.INFO, "VEHICLE_CONFIGURATION_OBSTACLE_ROUND_UNPARKING defined, setting coreControlState to UNPARK");
    coreControlState = UNPARK;
  #endif

  debugLogger.sendMessage("coreGetOrientation", debugLogger.INFO, "Set coreRoundDirCW to " + String(coreRoundDirCW ? "true" : "false")); 

}

void coreUnpark(){

  if(unparkAlgorithm.isFinished()){
    
    coreControlState = SAFE;
    return;

  }

  coreVehicleCommand = unparkAlgorithm.drive(coreVehicleData);
  coreVehicleCommandDirect = unparkAlgorithm.isDirectControl();
  coreVehicleInstructionToPi = NO_INSTRUCTION;

}

void coreDriveFromPi(){

  if(coreSerialCommand.instruction == RPI_RP2040_START_PARKING){
    
    coreControlState = PARK;
    coreVehicleInstructionToPi = RPI_RP2040_START_PARKING;
    return;

  }

  coreVehicleInstructionToPi = RP2040_RPI_START_OBSTACLE_NAVIGATION;
  coreVehicleCommand.targetSpeed = coreSerialCommand.targetSpeed;
  coreVehicleCommand.targetYaw = coreSerialCommand.targetYaw;
  coreVehicleCommandDirect = true;


}

void corePark(){

  if(parkAlgorithm.isFinished()){

    coreControlState = SAFE;
    return;

  }

  coreVehicleCommand = parkAlgorithm.drive(coreVehicleData);
  coreVehicleCommandDirect = parkAlgorithm.isDirectControl();

}

void coreSafe(){

  motor.driveMotor(0, false);
  motor.disarmMotor();
  steering.steer(0);

  while(true){

    for(int i = 0; i < 255; i += 5){

      RGBColor col;
      col.red = i;
      col.green = 0;
      col.blue = 0;

      rgbLED.setStaticColor(col);

    }

    for(int i = 0; i < 255; i += 5){

      RGBColor col;
      col.red = 0;
      col.green = i;
      col.blue = 0;

      rgbLED.setStaticColor(col);

    }

    for(int i = 0; i < 255; i += 5){

      RGBColor col;
      col.red = 0;
      col.green = 0;
      col.blue = i;

      rgbLED.setStaticColor(col);

    }

  }

}

void coreOpenRound(){

  if(openRoundAlgorithm.isFinished()){

    coreControlState = SAFE;
    return;

  }

  coreVehicleCommand = openRoundAlgorithm.drive(coreVehicleData);
  coreVehicleCommandDirect = openRoundAlgorithm.isDirectControl();

}

void coreRunStateMachine(){

  switch(coreControlState){

    case WAIT_FOR_BUTTON:
      coreWaitForButton();
      break;

    case OPEN_ROUND:
      coreOpenRound();
      break;

    case GET_ORIENTATION:
      coreGetOrientation();
      break;

    case UNPARK:
      coreUnpark();
      break;

    case DRIVE_FROM_PI:
      coreDriveFromPi();
      break;

    case PARK:
      corePark();
      break;

    case SAFE:
      coreSafe();
      break;

    default:
      coreSafe();   // Something has gone terribly wrong if we didn't match with any of the cases before us, so STOP!
      break;

  };

  coreSetLEDColor(coreControlState);

  debugLogger.sendMessage("coreRunStateMachine", debugLogger.INFO, "Core control state is " + coreGetStringFromState(coreControlState));

}

void coreSetLEDColor(CoreControlState state){
  
  rgbLED.limitBrightness(10);

  switch(state){

    case WAIT_FOR_BUTTON:
      rgbLED.setStaticColor(rgbLED.WHITE);
      break;

    case GET_ORIENTATION:
      rgbLED.setStaticColor(rgbLED.RED);
      break;

    case DRIVE_FROM_PI:
      rgbLED.setStaticColor(rgbLED.CYAN);
      break;

    case OPEN_ROUND:
      rgbLED.setStaticColor(rgbLED.AMBER);
      break;

    case PARK:
      rgbLED.setStaticColor(rgbLED.GREEN);
      break;

    case UNPARK:
      rgbLED.setStaticColor(rgbLED.GREEN);
      break;

    case SAFE:
      rgbLED.setStaticColor(rgbLED.PURPLE);
      break;

  }

}

void coreCheckSafeButton(){

  if(!digitalRead(VEHICLE_GET_CONFIG.pinConfig.lidarMotorPWM)){
    coreControlState = SAFE;
  }

}

String coreGetStringFromState(CoreControlState state){

  switch(state){

    case WAIT_FOR_BUTTON:
      return "WAIT_FOR_BUTTON";
      break;

    case GET_ORIENTATION:
      return "GET_ORIENTATION";
      break;

    case DRIVE_FROM_PI:
      return "DRIVE_FROM_PI";
      break;

    case OPEN_ROUND:
      return "OPEN_ROUND";
      break;

    case PARK:
      return "PARK";
      break;

    case UNPARK:
      return "UNPARK";
      break;

    case SAFE:
      return "SAFE";
      break;

  }

  return "Invalid State";

}

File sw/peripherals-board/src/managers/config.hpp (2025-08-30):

/**
 * @file configuration.hpp
 * @brief Defines various structs for holding configuration data
 * @author DIY Labs
 */

 #pragma once

#include <cstdint>
#include <Adafruit_BNO055.h>

class PowertrainDriver;

/**
 * @brief Phsyical pin numbers for peripherals
 */
struct PinConfig{

  uint8_t motorDriverPWM = 0;
  uint8_t motorDriverDirA = 0;
  uint8_t motorDriverDirB = 0; 
  uint8_t motorDriverStandby = 0;

  uint8_t motorEncoderA = 0;
  uint8_t motorEncoderB = 0;

  uint8_t steeringServo = 0;
  
  uint8_t nrfCS = 0;
  uint8_t nrfCE = 0;

  uint8_t i2c0SDA = 0;
  uint8_t i2c0SCL = 0;
  uint8_t i2c1SDA = 0;
  uint8_t i2c1SCL = 0;

  uint8_t spi0MOSI = 0;
  uint8_t spi0MISO = 0;
  uint8_t spi0SCK = 0;  

  uint8_t spi1MOSI = 0;
  uint8_t spi1MISO = 0;
  uint8_t spi1SCK = 0;  

  uint8_t uart0RX = 0;
  uint8_t uart0TX = 0;

  uint8_t uart1RX = 0;
  uint8_t uart1TX = 0;

  uint8_t lidarMotorPWM = 0;

  uint8_t rgbLed;

};

struct LimitsConfig{

  uint16_t maxForwardSpeed = 0;
  uint16_t maxReverseSpeed = 0;

  uint16_t servoMinOutput = 0;
  uint16_t servoMaxOutput = 0;
  uint16_t servoCenterOutput = 0;

};

struct ConstantsConfig{

  uint8_t ticksPerCM = 0;
  uint32_t debugSerialBaudRate = 0;
  uint32_t rpiSerialBaudRate = 0;

};

struct AddressConfig{

  uint8_t bnoAddr = 0;
  uint8_t leftLidarAddr = 0;
  uint8_t frontLidarAddr = 0;
  uint8_t rightLidarAddr = 0;
  uint8_t backLidarAddr = 0;

};

struct ControlConfig{

  double steeringP = 0;
  double steeringI = 0;
  double steeringD = 0;
  double maxSteeringPIDCommand = 0;
  double minSteeringPIDCommand = 0;

  double speedP = 0;
  double speedI = 0;
  double speedD = 0;
  double maxSpeedPIDCommand = 0;
  double minSpeedPIDCommand = 0;

  double maxSteeringAngle = 0;

  float servoCommandToOutputRatio = 1; // 1 to avoid division by zero errors
};

struct CalibrationConfig{

  adafruit_bno055_offsets_t imuOffsets;

};

/**
 * @brief One Config Struct To Rule Them All
 */
struct VehicleConfig{

  PinConfig pinConfig;
  LimitsConfig limitsConfig;
  ConstantsConfig constantsConfig;
  AddressConfig addressConfig;
  ControlConfig controlConfig;
  CalibrationConfig calibrationConfig;

};

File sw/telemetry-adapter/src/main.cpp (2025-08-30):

#include <Arduino.h>
#include <RF24.h>
#include <Adafruit_NeoPixel.h>
#include "pindefs.h"
#include "hwrev2_rf24_shared.hpp"


RF24 radio(RF_CE, RF_CSN);
Adafruit_NeoPixel pixel(1, PIN_RGB_LED, NEO_RGB + NEO_KHZ800);


unsigned long prevCommandSendTime = 0;
unsigned long commandSendIntervalMS = 10;

hwrev2_rf24_telem_block1 telemBlock1;
hwrev2_rf24_cmd_block1 cmdBlock1;

void blinkLED();
void printDataStruct();
void ledOn();
void ledOff();


void setup(){

  pixel.begin();
  pixel.setBrightness(5);

  SPI.setSCK(RF_SCK);
  SPI.setMOSI(RF_MOSI);
  SPI.setMISO(RF_MISO);

  if(!radio.begin()){
    pixel.setPixelColor(0, pixel.Color(255, 0, 0));
    pixel.show();
    while(true);
  }
  pixel.setPixelColor(0, pixel.Color(0, 255, 0));
  pixel.show();

  Serial.begin();  

  radio.setPALevel(RF24_PA_HIGH);
  radio.setDataRate(RF24_2MBPS);
  radio.setAutoAck(true);
  radio.enableAckPayload();
  radio.setAddressWidth(5);

  cmdBlock1.targetSpeed = 0;
  cmdBlock1.targetYaw = 90;
  
}

void loop(){

  radio.openReadingPipe(1, TLM_PIPE_0);
  radio.startListening();

  if(Serial.available()){

    String command = Serial.readStringUntil('\n');

    int commaIndex = command.indexOf(',');

    cmdBlock1.targetSpeed = constrain(command.substring(0, commaIndex).toInt(), -1024, 1024);
    cmdBlock1.targetYaw = constrain(command.substring(commaIndex + 1).toInt(), 0, 180);

  }

  uint8_t pipe;
  if(radio.available(&pipe)){

    radio.read(&telemBlock1, sizeof(telemBlock1));
    // Disable command code, don't have time to debug
    //radio.writeAckPayload(pipe, &cmdBlock1, sizeof(cmdBlock1));

    printDataStruct();

  }

}

void ledOn(){

  pixel.setPixelColor(0, pixel.Color(255, 255, 0));
  pixel.show();

}

void ledOff(){

  pixel.setPixelColor(0, pixel.Color(0, 0, 0));
  pixel.show();
  
}

void printDataStruct(){

  Serial.print(telemBlock1.millis);
  Serial.print(',');  

  Serial.print(telemBlock1.oriX);
  Serial.print(',');

  Serial.print(telemBlock1.lidarLeft);
  Serial.print(',');  

  Serial.print(telemBlock1.lidarFront);
  Serial.print(',');  

  Serial.print(telemBlock1.lidarRight);
  Serial.print(',');  

  Serial.print(telemBlock1.lidarBack);
  Serial.print(',');  

  Serial.print(telemBlock1.commandedSpeed);
  Serial.print(',');  

  Serial.print(telemBlock1.commandedSteer);
  Serial.print(',');  

  Serial.print(telemBlock1.roundDirectionCW);
  Serial.print(',');  

  Serial.println();

}

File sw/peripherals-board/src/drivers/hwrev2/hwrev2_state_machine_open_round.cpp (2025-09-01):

#include <hwrev2_state_machine_open_round.hpp>

hw_rev_2_StateMachineOpenRound::hw_rev_2_StateMachineOpenRound(VehicleConfig config){

  _cfg = config;

}

void hw_rev_2_StateMachineOpenRound::init(ILogger *logger){

  _logger = logger;
  _state = GET_START_DIST;

}

VehicleCommand hw_rev_2_StateMachineOpenRound::drive(VehicleData vehicleData){

  _data = vehicleData;

  switch(_state){

    case GET_START_DIST:
      _getStartDist();
      break;

    case INITIAL_STRAIGHT:
      _initialStraight();
      break;

    case GET_ROUND_DIR:
      _getRoundDir();
      break;

    case INITIAL_MOVE_BACKWARD:
      _initialMoveBackward();
      break;

    case STRAIGHT_0:
      _straight0();
      break;

    case STRAIGHT_90:
      _straight90();
      break;

    case STRAIGHT_180:
      _straight180();
      break;

    case STRAIGHT_270:
      _straight270();
      break;

  }

  return _cmd;

}

void hw_rev_2_StateMachineOpenRound::_getStartDist(){

  _frontStartDist = _data.lidar[0];
  _state = INITIAL_STRAIGHT;

  _cmd.targetSpeed = 0;
  _cmd.targetYaw = 90;

}

void hw_rev_2_StateMachineOpenRound::_initialStraight(){

  if(_data.lidar[0] <= _frontProbeThreshold){
 
    _cmd.targetSpeed = 0;
    _cmd.targetYaw = 90;
    _state = GET_ROUND_DIR;
    return;

  }

  _cmd.targetYaw = _steeringController(_data.orientation.x, 0);
  _cmd.targetSpeed = _absSlowSpeed;

}

void hw_rev_2_StateMachineOpenRound::_getRoundDir(){

  uint16_t leftDist = _data.lidar[270];
  uint16_t rightDist = _data.lidar[90];

  _roundDirCW = rightDist > leftDist;

  _logger->sendMessage("hw_rev_2_StateMachineOpenRound::_getRoundDir", _logger->INFO, "Left distance: " + String(leftDist) + ", right distance: " + String(rightDist) + ", _roundDirCW: " + String(_roundDirCW));

  _cmd.targetYaw = 90;
  _cmd.targetSpeed = 0;
  _state = INITIAL_MOVE_BACKWARD;

}

void hw_rev_2_StateMachineOpenRound::_initialMoveBackward(){

  if(_data.lidar[0] >= _frontTurnThreshold){
    
    _cmd.targetYaw = 90;
    _cmd.targetSpeed = 0;
    _state = STRAIGHT_0;
    return;

  }

  _cmd.targetSpeed = -_absSlowSpeed;
  _cmd.targetYaw = 90;

}

void hw_rev_2_StateMachineOpenRound::_straight0(){

  if(_data.lidar[0] <= _frontTurnThreshold && _inDegreeRange(_data.orientation.x, 0, turnMargin)){
    _state = _roundDirCW ? STRAIGHT_90 : STRAIGHT_270;
    _numTurns++;
    return;
  }

  _cmd.targetYaw = _steeringController(_data.orientation.x, 0);  

  _speedCheck();
  _stopCheck();

}

void hw_rev_2_StateMachineOpenRound::_straight90(){

  if(_data.lidar[0] <= _frontTurnThreshold && _inDegreeRange(_data.orientation.x, 90, turnMargin)){
    _state = _roundDirCW ? STRAIGHT_180 : STRAIGHT_0;
    _numTurns++;
    return;
  }

  _cmd.targetYaw = _steeringController(_data.orientation.x, 90);  
  _cmd.targetSpeed = _absBaseSpeed;

  _speedCheck();
  _stopCheck();

}

void hw_rev_2_StateMachineOpenRound::_straight180(){

  if(_data.lidar[0] <= _frontTurnThreshold && _inDegreeRange(_data.orientation.x, 180, turnMargin)){
    _state = _roundDirCW ? STRAIGHT_270 : STRAIGHT_90;
    _numTurns++;
    return;
  }

  _cmd.targetYaw = _steeringController(_data.orientation.x, 180);  
  _cmd.targetSpeed = _absBaseSpeed;

  _speedCheck();
  _stopCheck();

}

void hw_rev_2_StateMachineOpenRound::_straight270(){

  if(_data.lidar[0] <= _frontTurnThreshold && _inDegreeRange(_data.orientation.x, 270, turnMargin)){
    _state = _roundDirCW ? STRAIGHT_0 : STRAIGHT_180;
    _numTurns++;
    return;
  }

  _cmd.targetYaw = _steeringController(_data.orientation.x, 270);  
  _cmd.targetSpeed = _absBaseSpeed;

  _speedCheck();
  _stopCheck();

}

int16_t hw_rev_2_StateMachineOpenRound::_steeringController(double current, double target){

  double error = target - current;
  double proportionalOutput;
  double integralOutput;
  double totalOutput;
  double servoOutput;
  static double errorSum;

  if(error > 180){
    error -= 360;
  }
  else if(error < -180){
    error += 360;
  }

  proportionalOutput = error * _kP;
  integralOutput = errorSum * _kI;

  totalOutput = proportionalOutput + integralOutput;

  servoOutput = 90 + totalOutput;
  servoOutput =  constrain(servoOutput, 20, 160);

  return servoOutput;

}

bool hw_rev_2_StateMachineOpenRound::_inDegreeRange(double degree, double target, double range){

  degree = fmod(fmod(degree, 360.0) + 360.0, 360.0);
  target = fmod(fmod(target, 360.0) + 360.0, 360.0);
  double diff = abs(degree - target);

  if(diff > 180){
    diff = 360 - diff;
  }

  return diff <= range;

}

void hw_rev_2_StateMachineOpenRound::_stopCheck(){

  if(_numTurns >= 12 && _inDegreeRange(_data.orientation.x, 0, turnMargin)){  

    if(_data.lidar[0] < _frontStartDist){

      _cmd.targetSpeed = 0;
      _cmd.targetYaw = 90;
      _state = COMPLETED;

    }

  }

}

void hw_rev_2_StateMachineOpenRound::_speedCheck(){

  if(_numTurns == 12){  

    _cmd.targetSpeed = _absBaseSpeed;

  }
  else{

    _cmd.targetSpeed = _absBaseSpeed;

  }

}

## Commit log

2025-08-26 Update LiDAR holders to counter angle of chassis
    [Lidar Holder V3.stl, Rear Lidar Mount.stl]
2025-08-26 Wrong file was uploaded
    [Lidar Holder V2.stl, Lidar Holder V3.stl]
2025-08-26 Single red obstacles successfully avoided
    [basic-nav-v2.py]
2025-08-27 This one doesn't work yet
    [exit-parking.py]
2025-08-28 IMplement parking driver
2025-08-28 Add command parsing to debug port, add CYAN color to RGB LED driver
2025-08-28 Set up logger for peripherls board data
2025-08-28 UNTESTED: Implement state machine for main code flow, switch between algorithms for driving
2025-08-28 Working switching logic in main
2025-08-28 Questionable formatting to make editing and reading easier 😁
2025-08-29 Update README and files to not use RPLidar
    [Lidar Holder V2.stl, Lidar Holder V3.stl]
2025-08-29 Add raw photos of vehicle assembly
2025-08-29 Updated design files
    [Lidar Holder V3.stl, Lidar Holder V4.stl, Rear Lidar Mount.stl]
2025-08-29 Increase steering limits in open round algorithm
2025-08-29 Change LED color based on state
2025-08-29 Swap order in serial comm driver; data is sent if a command is received
    [hwrev2_serial_communication.cpp, main.cpp]
2025-08-29 Remove steering angle limit in steering driver
2025-08-29 Robot assembly photos link
2025-08-30 Longer rear lidar holder to make parking easier
    [Rear Lidar Mount-Long.stl]
2025-08-31 Clean up open round code, bug fixes
    [hwrev2_single_lidar_open_round.cpp, hwrev2_single_lidar_open_round.hpp]
2025-08-31 Make lidar holder stronger
    [Lidar Holder V4.stl]
2025-09-01 Add start button support, use preprocessor defines to switch between sequences
2025-09-01 Update wording of BOM, add section for peripherals board interface in packing checklist
2025-09-01 Switch to state machine open round, move state machine open round .cpp file into hwrev2 driver folder
2025-09-01 Improper previous design
    [Lidar Holder V4.stl]
2025-09-01 Remove PID control from state machine open round algorithm
2025-09-01 Tuned state-machine open-round algorithm, fixed clockwise
    [hwrev2_state_machine_open_round.cpp, main.cpp]
2025-09-04 Remove obstaclle round without unparking case, add RGB pulses on RGB LED for SAFE cond
2025-09-05 Print core control state and target yaw over debug port
2025-09-05 Compile open round with more debug prints
2025-09-05 Add delay if button is pressed
